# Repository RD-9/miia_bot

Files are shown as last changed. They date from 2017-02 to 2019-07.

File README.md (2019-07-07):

# Welcome MiiA Coders
Congratulations on obtaining your MiiA bot.These instructions will take you through everything you need to know on how MiiA bot is put together and what makes her tick. MiiA botis built in the form of a 3D puzzle, so the fun begins immediately. The MiiA design is based off of another great robot called Otto (https://www.ottodiy.com). We have completely open sourced the MiiA bot design under the Creative Commons  license. So without further ado, let’s jump in!
e
# CAD files
As mentioned, all the design files for Miia bot has been open sourced and can be found in the assembly folder. 
# Assembly
The cad files along with the assembly instructions is found in the assembly folder. This is to help with putting MiiA bot's physical structure together. 
# Getting started
Once the physical robot has been put together, go to the exercise folder to find the getting started guide. This will help you to connect to the Lofi Blocks programming platform and get you started quickly. 
# Exercise sheet
Once MiiA has been connected to the Lofi Blocks platform, the exercise sheets should be worked through.These exercises should be worked through with the video tutorials. This will help you to understand the steps needed when programming MiiA.It will also help you to understand the process of thinking through the problem when creating your own functions.
# Challenge
The final challenge combines all the lessons from the individual exercises. These challenges can be found in the exercise folder.New challenges will be added in order to test your robot skills, so stay tuned.

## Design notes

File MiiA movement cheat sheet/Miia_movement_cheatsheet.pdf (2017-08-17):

Movement name | Steps | Motor A | Motor B | Motor C | Motor D | loop | Notes
Motor position | | left ankle | right ankle | left hip | right hip
Output number | | output1 | output2 | output3 | output4
Stand left leg | Step 1 | 120 | 170 | 90 | 90
Stand right leg | Step 1 | 10 | 60 | 90 | 90
Walk forward (left foot step) | Step 1 | 120 | 170 | 90 | 90
| Step 2 | 120 | 170 | 120 | 120
| Step 3 | 90 | 90 | 120 | 120
Walk forward (right foot step) | step 1 | 10 | 60 | 90 | 90
| step 2 | 10 | 60 | 60 | 60
| step 3 | 90 | 90 | 60 | 60 | loop left step -right step
Walk back (left foot step) | Step 1 | 120 | 170 | 90 | 90
| Step 2 | 120 | 170 | 60 | 60
| Step 3 | 90 | 90 | 60 | 60
Walk back (right foot step) | step 1 | 10 | 60 | 90 | 90
| step 2 | 10 | 60 | 120 | 120
| step 3 | 90 | 90 | 120 | 120 | loop left step -right step
Turn left forward | Step 1 | 90 | 90 | 90 | 90
| Step 2 | 120 | 170 | 90 | 90
| Step 3 | 120 | 90 | 90 | 90
| Step 4 | 120 | 90 | 130 | 90
| Step 5 | 90 | 90 | 130 | 90
Turn left back | Step 1 | 90 | 90 | 90 | 90
| Step 2 | 120 | 170 | 90 | 90
| Step 3 | 120 | 90 | 90 | 90
| Step 4 | 120 | 90 | 50 | 90
| Step 5 | 90 | 90 | 50 | 90
Turn right forward | Step 1 | 90 | 90 | 90 | 90

| Step 2 | 10 | 60 | 90 | 90
| Step 3 | 90 | 60 | 90 | 90
| Step 4 | 90 | 60 | 90 | 50
| Step 5 | 90 | 90 | 90 | 50
Turn right back | Step 1 | 90 | 90 | 90 | 90
| Step 2 | 10 | 60 | 90 | 90
| Step 3 | 90 | 60 | 90 | 90
| Step 4 | 90 | 60 | 90 | 130
| Step 5 | 90 | 90 | 90 | 130
Hip roll forward | Step 1 | 90 | 90 | 110 | 70
| Step 2 | 90 | 90 | 90 | 90 | loop 1 and 2
Hip roll forward | Step 1 | 90 | 90 | 70 | 110 | | Each leg can be changed individually while leaving the other at 90
| Step 2 | 90 | 90 | 90 | 90 | loop 1 and 2
Foot tap left | Step 1 | 110 | 90 | 90 | 90
| Step 2 | 90 | 90 | 90 | 90 | loop 1 and 2
Foot tap right | Step 1 | 90 | 70 | 90 | 90
| Step 2 | 90 | 90 | 90 | 90 | loop 1 and 2
Foot wave right | Step 1 | 120 | 170 | 90 | 90
| Step 2 | 120 | 70 | 90 | 90
| Step 3 | 120 | 120 | 90 | 90 | loop 2 and 3
Foot wave left | Step 1 | 10 | 60 | 90 | 90
| Step 2 | 120 | 60 | 90 | 90
| Step 3 | 70 | 60 | 90 | 90 | loop 2 and 3
heal stand | Step 1 | 160 | 20 | 90 | 90
toe stand | Step 1 | 20 | 160 | 90 | 90
initial stand | Step 1 | 90 | 90 | 90 | 90

Note: input a wait of 1000 after each step

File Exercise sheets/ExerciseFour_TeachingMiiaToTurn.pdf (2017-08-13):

# Exercise four: MiiA Turning time

## Aim:

### What good is a robot that can only go straight? Not very useful I would say. This

sheet will help with that. The steps to Turn MiiA left and right will be developed.

Note: There are many ways to do this. We do it in four steps, however, you could get it down to three steps (think about the things you do when you turn you turn).

### Forward

### Turn left

| | Motor A | Motor B | Motor C | Motor D
Step one | Angle
Step two | Angle
Step three | Angle
Step four | Angle
Notes

### Turn Right

| | Motor A | Motor B | Motor C | Motor D
Step one | Angle
Step two | Angle
Step three | Angle
Step four | Angle
Notes

### Backwards

### Turn left

| | Motor A | Motor B | Motor C | Motor D
Step one | Angle
Step two | Angle
Step three | Angle
Step four | Angle
Notes

### Turn Right

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

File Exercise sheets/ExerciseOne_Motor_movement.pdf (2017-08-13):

# Exercise one: MiiA motor movements

Aim:
This sheet will help investigate the different angles and movement of the servo motors. Change the angle of the motors from 1 to 180. Write down the direction the feet and hips move.

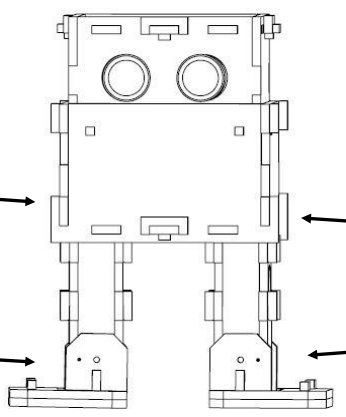
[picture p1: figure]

Foot movements
Foot | Output | Up | Down
Motor A
Motor B

Hip movements
Hips | Output | Forward | Back
Motor C
Motor D

(C)

### Left hip

(D)

### Right hip

(B)

### Right Ankle

(A)

### Left Ankle

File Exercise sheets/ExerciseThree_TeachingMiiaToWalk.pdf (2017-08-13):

# Exercise three: MiiA First steps

## Aim:

One of the first things we would want to do is getting MiiA walking. This exercise will help you make MiiA take those first steps.

## Hint: the step consists of 3 stages (Think of the way you walk, what are those stages).Important questions to ask are: How will you take 2 steps? How will you take many steps?

## Walk

### Forward – step with left leg

| | Motor A | Motor B | Motor C | Motor D
Step one | Angle
Step two | Angle
Step three | Angle
Notes

### Forward – step with Right leg

| | Motor A | Motor B | Motor C | Motor D
Step one | Angle
Step two | Angle
Step three | Angle
Notes

### Forward – Combine for two steps

| | Motor A | Motor B | Motor C | Motor D
Step one | Angle
Step two | Angle
Step three | Angle
Step four | Angle
Step five | Angle
Step six | Angle
Notes

Hint: two steps can be looped for as many steps as you want

At this point you should have gotten MiiA to walk forward. Great job!

Now to extend this to make MiiA walk back. This shouldn’t take too long. It’s the same thing, but different

## Walk Back

### Back – step with left leg

| | Motor A | Motor B | Motor C | Motor D
Step one | Angle
Step two | Angle
Step three | Angle
Notes

### Back – step with Right leg

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

### Back– Combine for two steps

| | Motor A | Motor B | Motor C | Motor D
Step one | Angle
Step two | Angle
Step three | Angle
Step four | Angle
Step five | Angle
Step six | Angle
Notes

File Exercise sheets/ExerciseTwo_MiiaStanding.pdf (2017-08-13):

# Exercise two: MiiA standing exercise

### Aim:

This sheet will help you to find the optimum angles which will make MiiA stand. Standing on one leg is the first step to many moves so it is important to ensure that the motors are in the optimum positions.

Hint: Only the two ankle servos are needed. (Motor C and D is set to 90 degrees)

Stand - Right foot

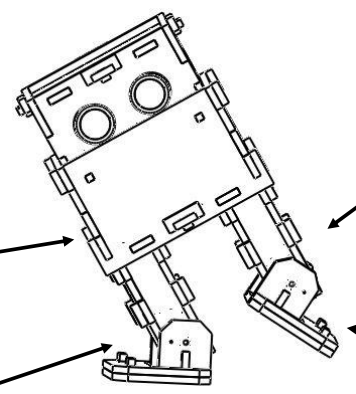
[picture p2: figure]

| Motor A | Motor B | Motor C | Motor D
Angle | | | 90 | 90
Notes

Stand - Left foot

| Motor A | Motor B | Motor C | Motor D
Angle | | | 90 | 90
Notes

(C)

### Left hip

(D)

### Right hip

(B)

### Right Ankle

(A)

### Left Ankle

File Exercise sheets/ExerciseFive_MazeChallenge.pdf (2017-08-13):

# Exercise five: MiiA Maze Challenge

Aim:
The aim of this exercise is to test the performance of the code developed.

Objective
Code the functions for your robot controller in any way you feel fit using the Lofi platform. The objective of this challenge is to navigate through a maze from one side to the other using the coded controller.

Hint: To construct the controller follow the steps in the Miia Controller construction_Exercise Five - Part 7.mp4 Video.

Instruction
- Get from the start to finish as quickly as possible
- The robot should walk over the boundaries, if this happens they should be brought back before the boundary
- The time starts once the robot has crossed the start line
- The robot can be righted if it has fallen over. However this will result in a penalty. It also should not be placed further in the maze.
- All the checkpoints should be entered before going to the finish line and time penalties will be imposed if this is not done.

Scoring
- The robot that navigates the maze the quickest wins.
- 10 seconds is added ever time the robot falls over and needs to be righted manually
- No time penalty is imposed if the robot walks over a boundary, however the robot needs to be brought back before continuing with the course.
- 2 minute is added to the time for each checkpoint not reached.

Proposed Maze

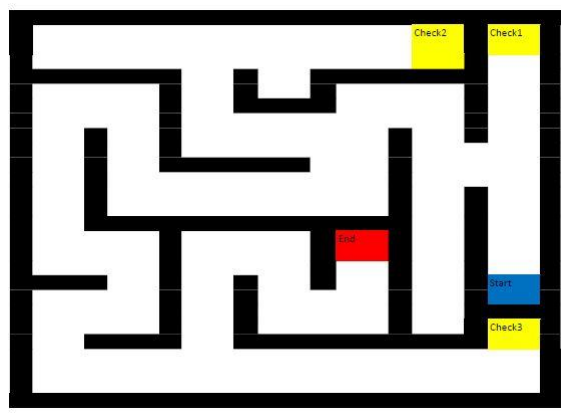
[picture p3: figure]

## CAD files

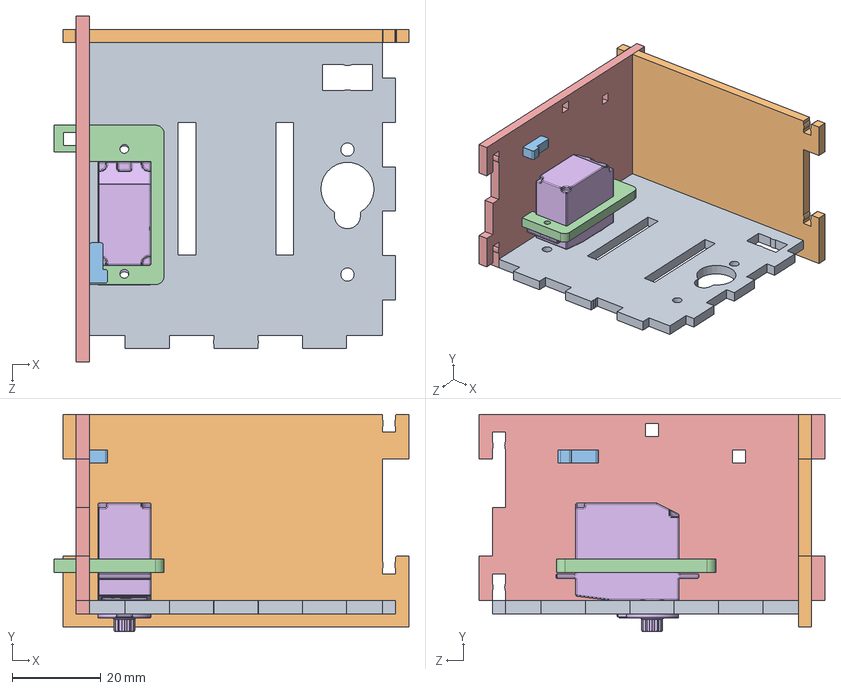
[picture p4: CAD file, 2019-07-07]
Assembly Instructions/Miia_bot_cadfiles/Bottom/Bottom_assemV2.SLDASM
80.1 x 49.0 x 78.1 mm
Bottom_bodyV2
Bottom_frontalsV2
PinGeneral
ServoMountV2
Bottom_sidesRV2
MICRO SERVO 9g

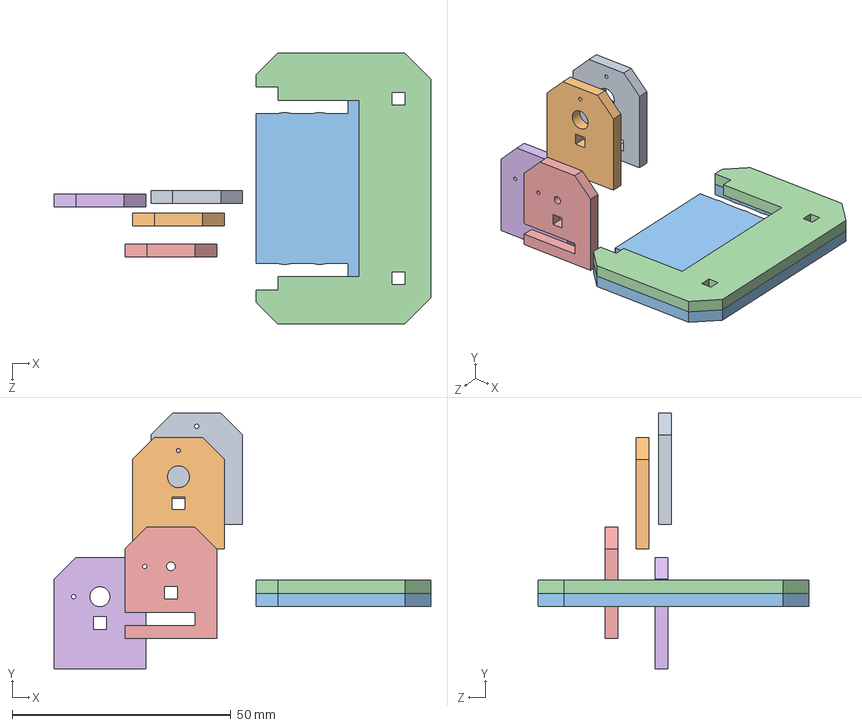
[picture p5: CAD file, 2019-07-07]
Assembly Instructions/Miia_bot_cadfiles/Foot/foot_assemV2.SLDASM
86.2 x 58.5 x 62.0 mm
backbrackethookV2
backbracketV2
Foot_botV2
foot_topV2
FrontbrackethookV2
frontbracketV2

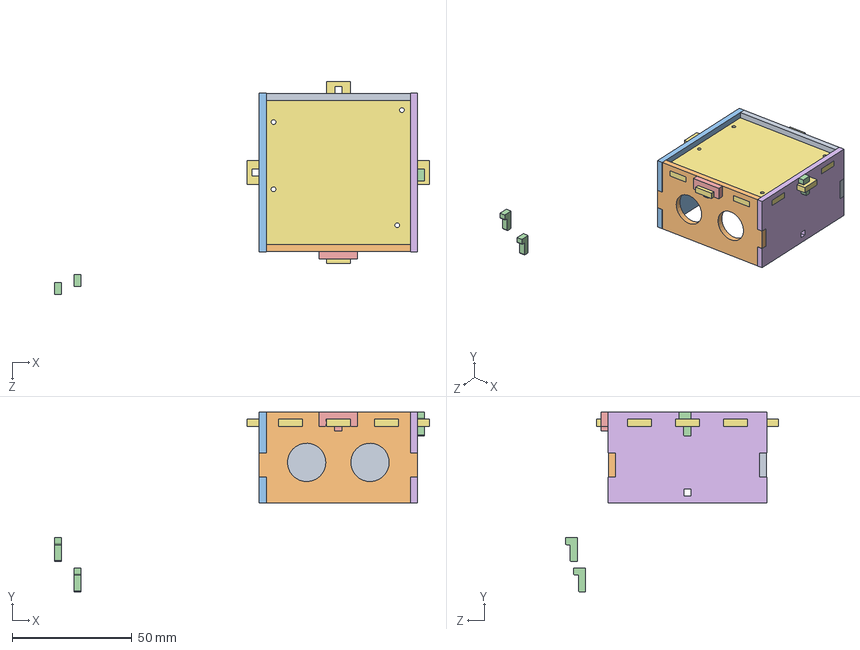
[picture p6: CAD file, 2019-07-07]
Assembly Instructions/Miia_bot_cadfiles/Head/Head_assemV2.SLDASM
156.3 x 75.0 x 88.9 mm
head_backV2
head_frontV2
head_leftV2
head_pintwoV2 x 3
head_pinV2
head_rightV2
Head_topV2

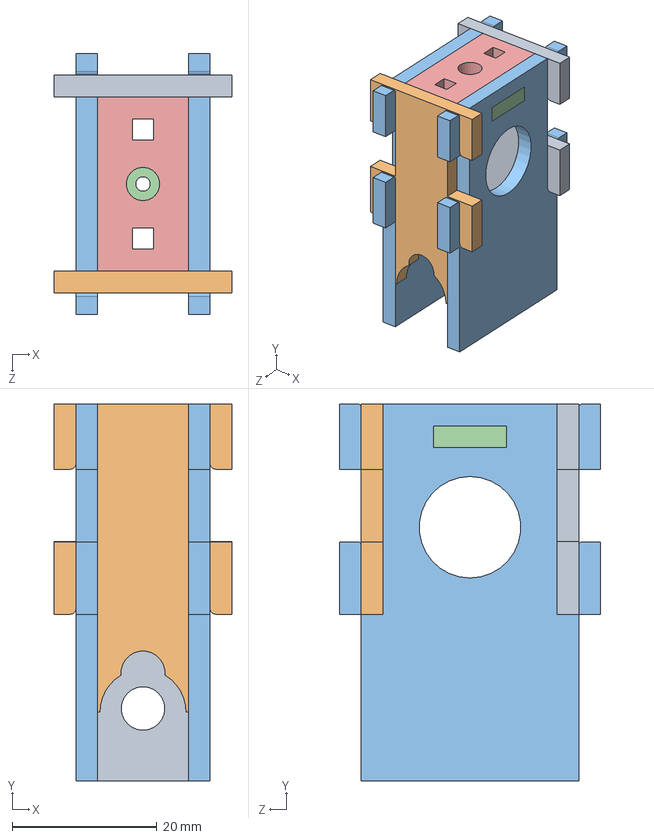
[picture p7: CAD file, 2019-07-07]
Assembly Instructions/Miia_bot_cadfiles/Legs/Leg_AssemV2.SLDASM
24.5 x 52.0 x 36.0 mm
backV2
FrontlV2
sideV2 x 2
topbotV2
topV2

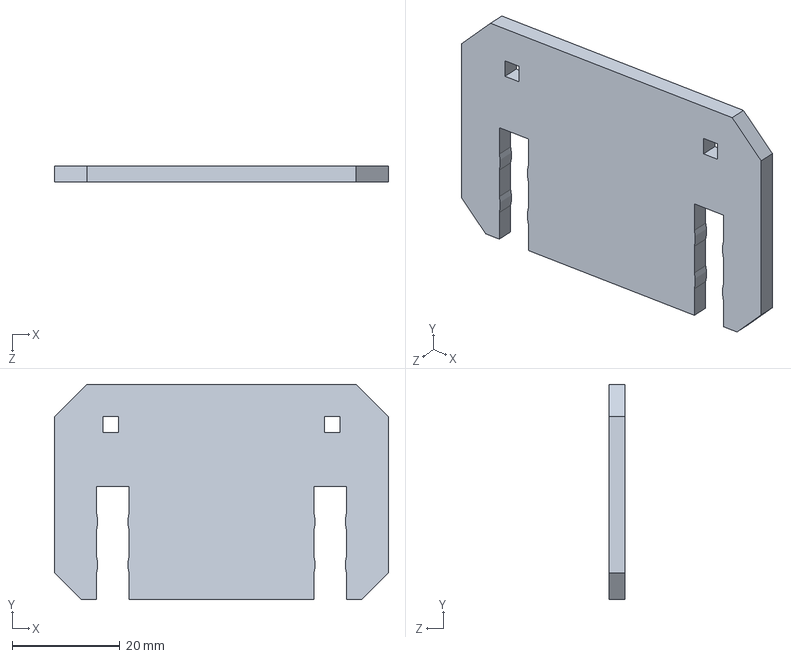
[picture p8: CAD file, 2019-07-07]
Assembly Instructions/Miia_bot_cadfiles/Foot/Foot_botV2.SLDPRT
62.0 x 40.0 x 3.00 mm

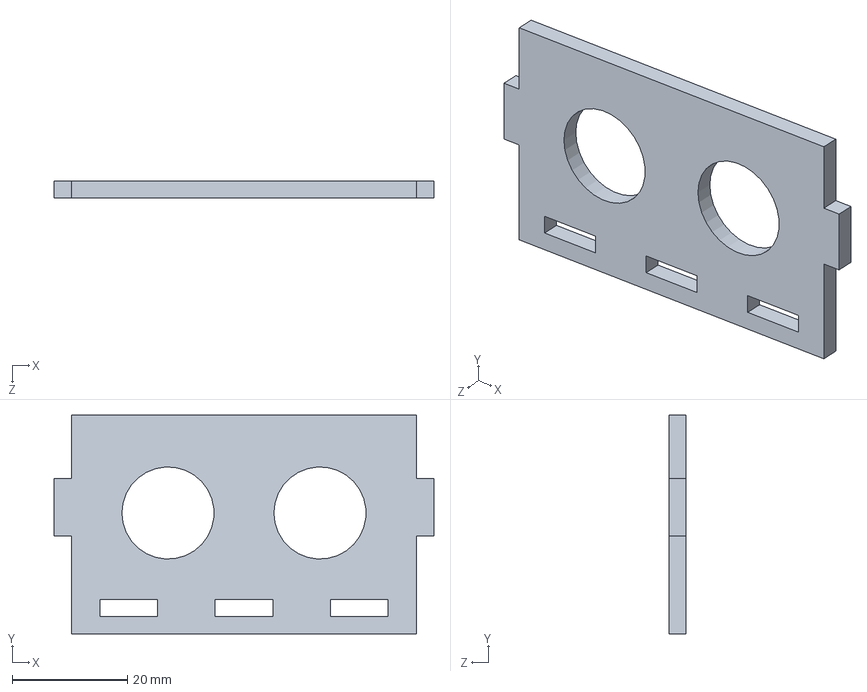
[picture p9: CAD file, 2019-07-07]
Assembly Instructions/Miia_bot_cadfiles/Head/head_frontV2.SLDPRT
66.0 x 38.0 x 3.00 mm

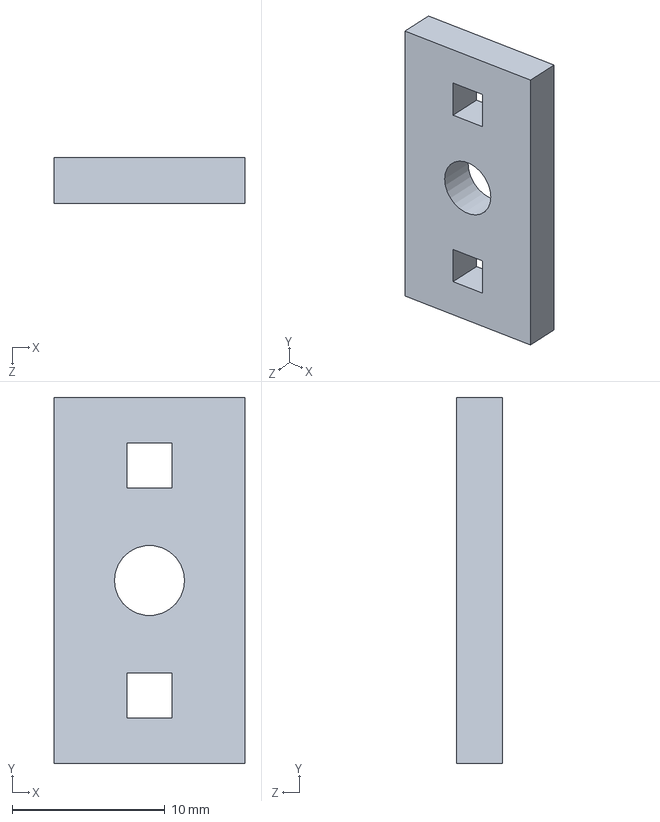
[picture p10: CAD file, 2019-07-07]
Assembly Instructions/Miia_bot_cadfiles/Legs/topV2.SLDPRT
12.5 x 24.0 x 3.00 mm

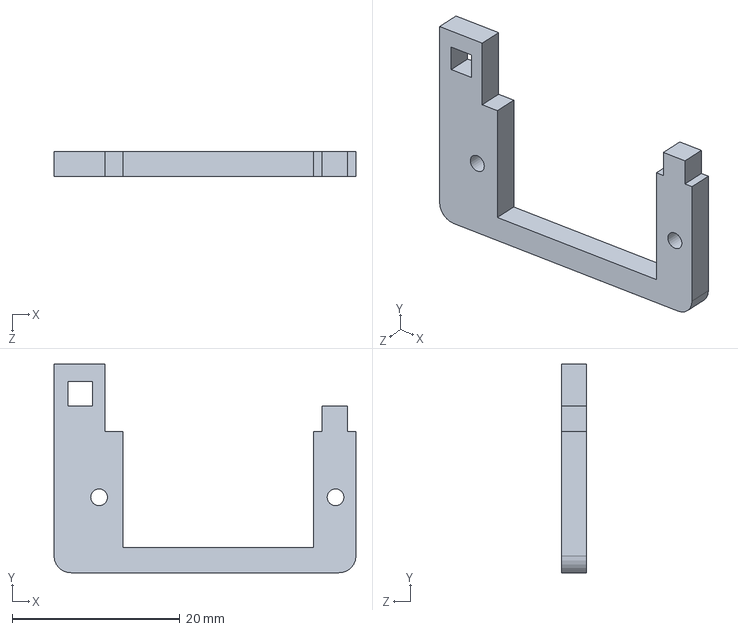
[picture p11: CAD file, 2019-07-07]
Assembly Instructions/Miia_bot_cadfiles/Bottom/ServoMountV2.SLDPRT
36.0 x 24.9 x 3.00 mm

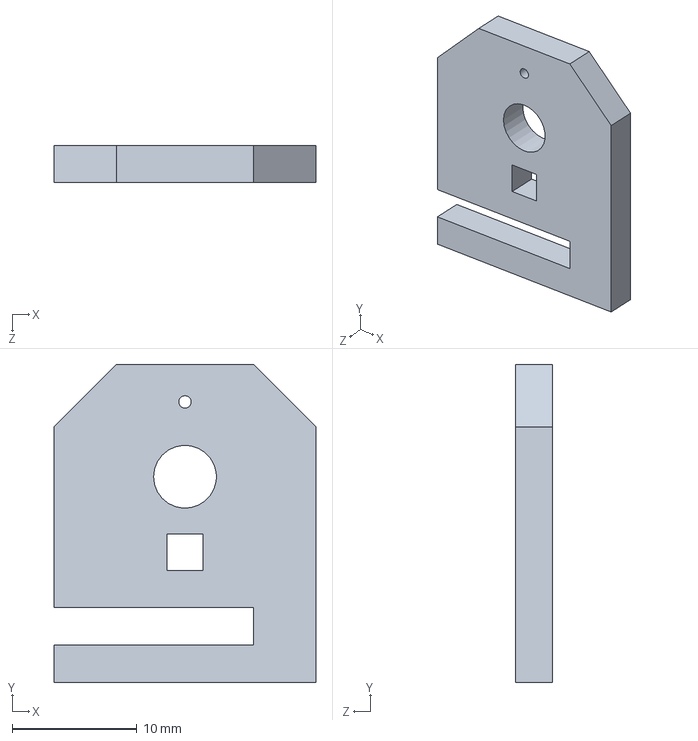
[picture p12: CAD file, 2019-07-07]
Assembly Instructions/Miia_bot_cadfiles/Foot/backbrackethookV2.SLDPRT
21.0 x 25.5 x 3.00 mm

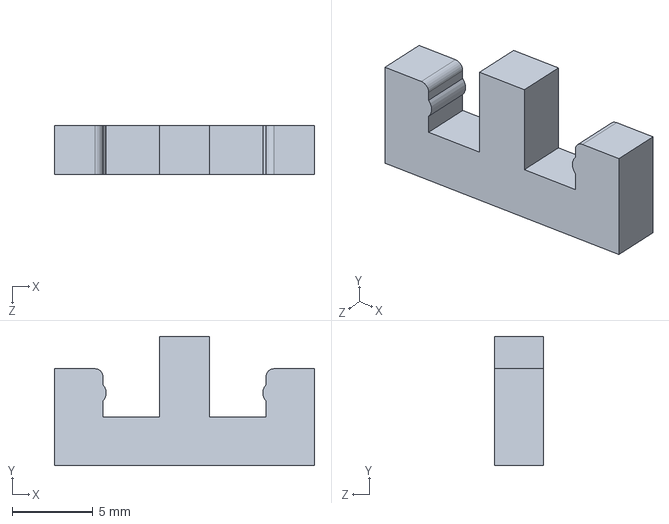
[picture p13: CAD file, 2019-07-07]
Assembly Instructions/Miia_bot_cadfiles/Head/head_pinV2.SLDPRT
16.1 x 8.00 x 3.00 mm

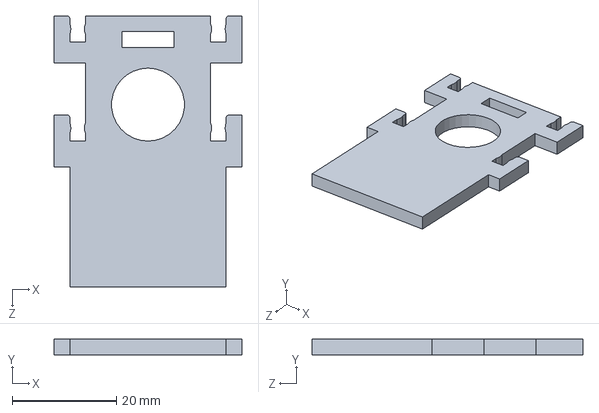
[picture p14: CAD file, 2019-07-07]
Assembly Instructions/Miia_bot_cadfiles/Legs/sideV2.SLDPRT
36.0 x 3.00 x 52.0 mm

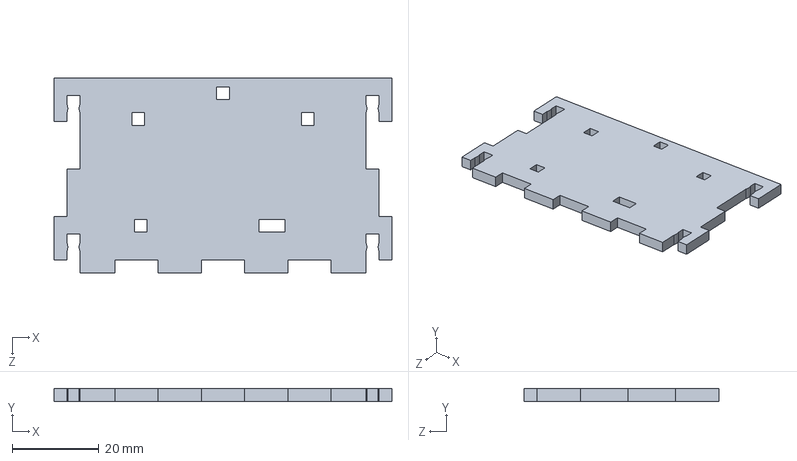
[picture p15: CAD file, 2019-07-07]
Assembly Instructions/Miia_bot_cadfiles/Bottom/Bottom_sidesRV2.SLDPRT
78.1 x 3.00 x 45.0 mm

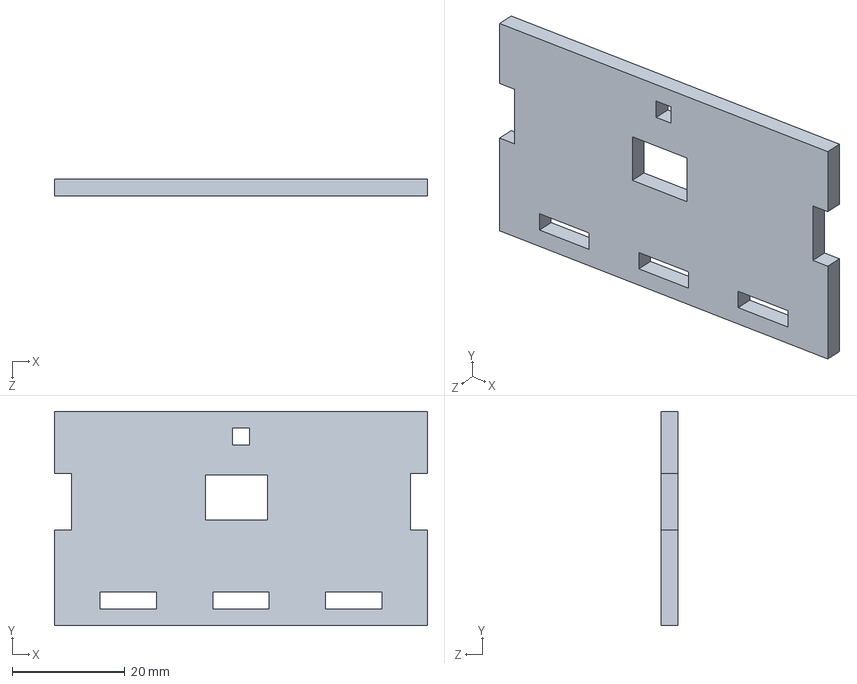
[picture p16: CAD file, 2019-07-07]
Assembly Instructions/Miia_bot_cadfiles/Head/head_leftV2.SLDPRT
66.1 x 38.0 x 3.00 mm

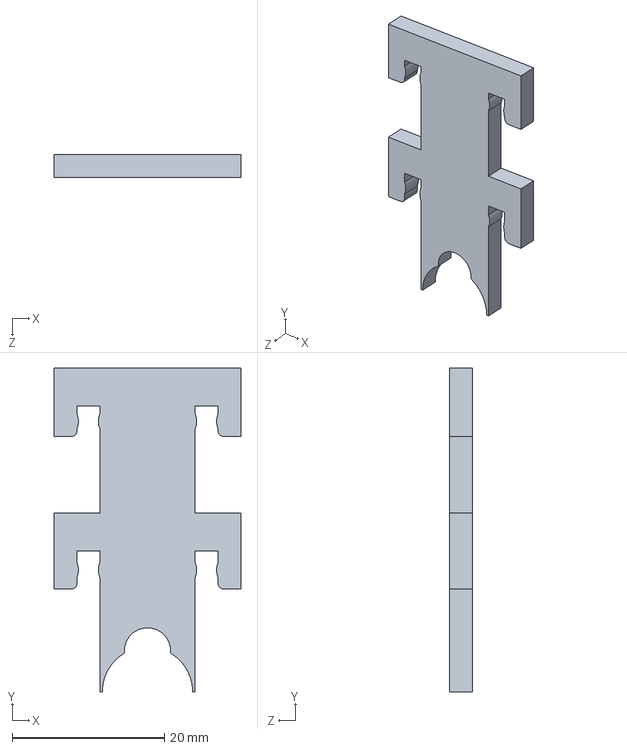
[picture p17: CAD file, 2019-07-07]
Assembly Instructions/Miia_bot_cadfiles/Legs/FrontlV2.SLDPRT
24.5 x 42.5 x 3.00 mm

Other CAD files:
Assembly Instructions/Miia_bot_cadfiles/Bottom/Bottom_bodyV2.SLDPRT
Assembly Instructions/Miia_bot_cadfiles/Foot/frontbracketV2.SLDPRT
Assembly Instructions/Miia_bot_cadfiles/Head/head_pintwoV2.SLDPRT
Assembly Instructions/Miia_bot_cadfiles/Legs/topbotV2.SLDPRT
Assembly Instructions/Miia_bot_cadfiles/Bottom/Bottom_frontalsV2.SLDPRT
Assembly Instructions/Miia_bot_cadfiles/Bottom/PinGeneral.SLDPRT
Assembly Instructions/Miia_bot_cadfiles/Bottom/PinGeneralV2.SLDPRT
Assembly Instructions/Miia_bot_cadfiles/Drawing/Manufacture.SLDDRW
Assembly Instructions/Miia_bot_cadfiles/Foot/FrontbrackethookV2.SLDPRT
Assembly Instructions/Miia_bot_cadfiles/Foot/backbracketV2.SLDPRT
Assembly Instructions/Miia_bot_cadfiles/Foot/foot_topV2.SLDPRT
Assembly Instructions/Miia_bot_cadfiles/Head/Head_topV2.SLDPRT
Assembly Instructions/Miia_bot_cadfiles/Head/head_backV2.SLDPRT
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

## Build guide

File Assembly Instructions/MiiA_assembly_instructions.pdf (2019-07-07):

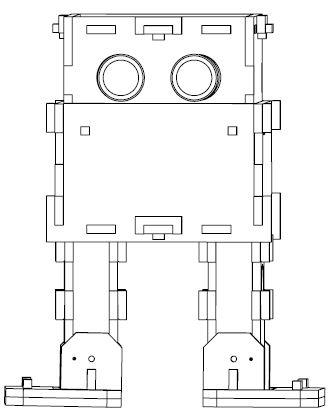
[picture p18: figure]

# MIIA ASSEMBLY INSTRUCTIONS

### WELCOME

Congratulations! You are now the proud new owner of your own MiiA robot. These instructions will take you through everything you need to know on how MiiA is put together and what makes her tick. MiiA is built in the form of a 3D puzzle, so the fun begins immediately. The MiiA bot design is based off another great robot called Otto bot (https://www.ottodiy.com). So, without further ado, let’s jump in!

## Contents

## What’s in the Box

All parts included in the kit are shown in this section.

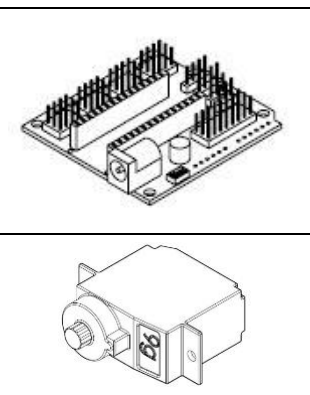
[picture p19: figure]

Part | Preview | Part | Preview
Battery holder (1x) | | Arduino shield (1x)
HC06 Bluetooth transceiver (1x) | | Servo Motor (4x)

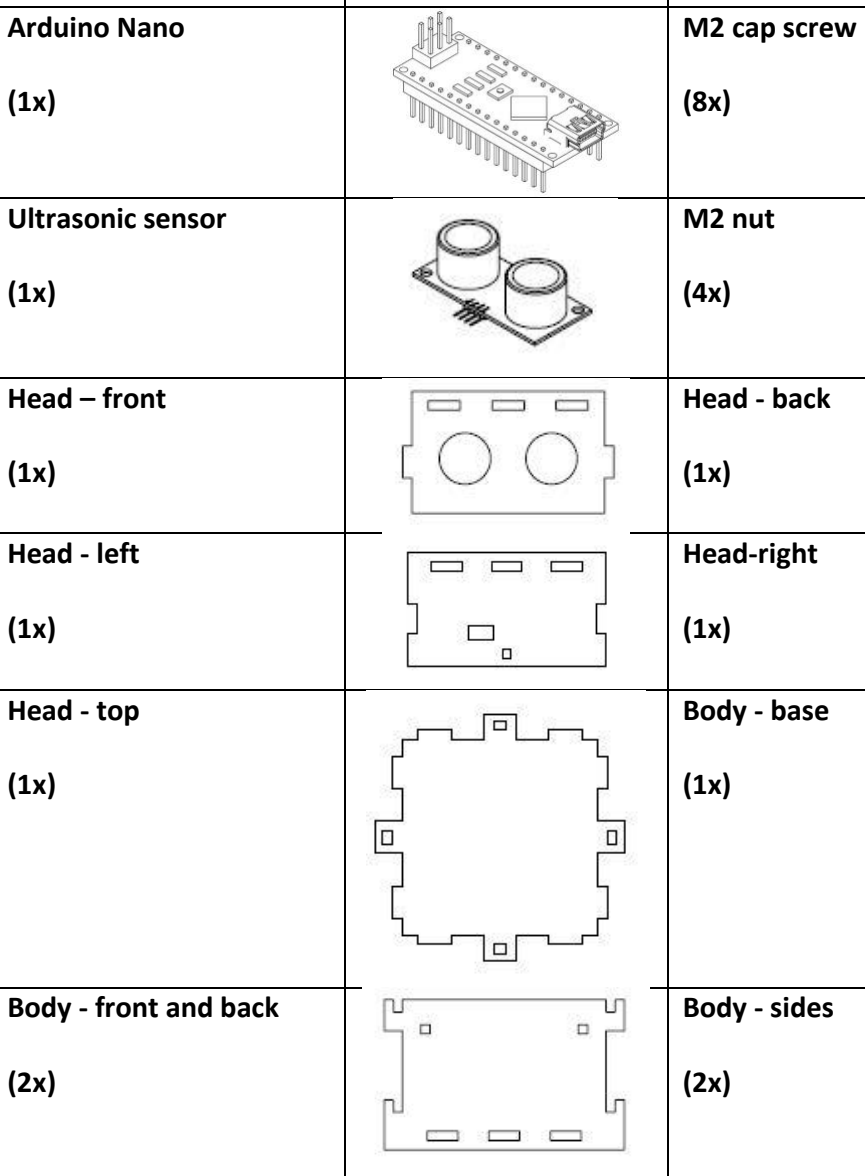
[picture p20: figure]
Arduino Nano (1x); M2 cap screw (8x); Ultrasonic sensor (1x); M2 nut (4x); Head – front (1x); Head - back (1x); Head - left (1x); Head-right (1x); Head - top (1x); Body - base (1x)
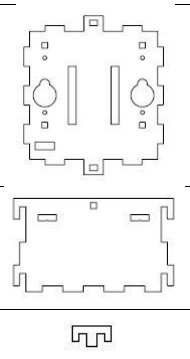
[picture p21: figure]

Body - front and back (2x) | | Body - sides (2x)
Body - corners (4x) | | Head and body pin (6x)

General pin (12x) | Leg - top (2x)
Leg - bottom plate (2x) | Leg - front (2x)

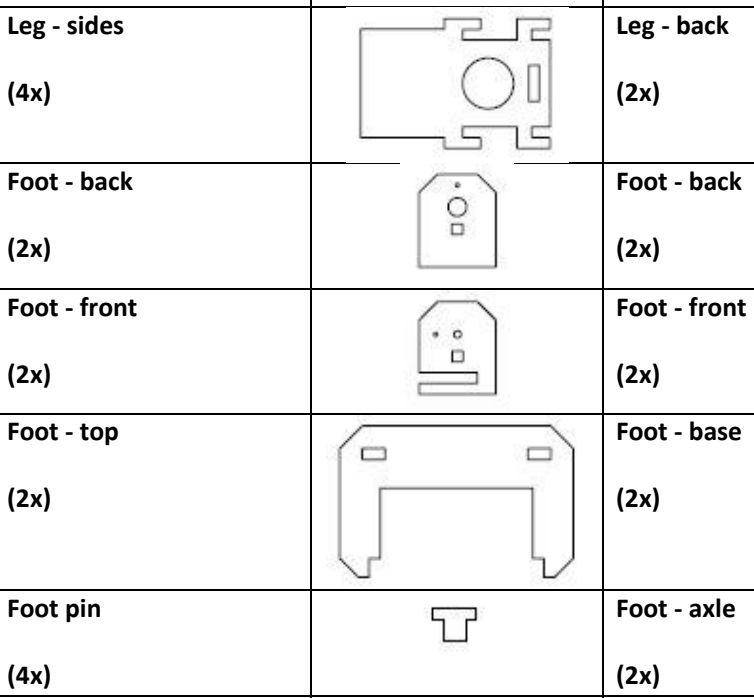
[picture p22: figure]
Leg - sides (4x); Leg - back (2x); Foot - back (2x); Foot - front (2x); Foot - top (2x); Foot - base (2x); Foot pin (4x); Foot - axle (2x)
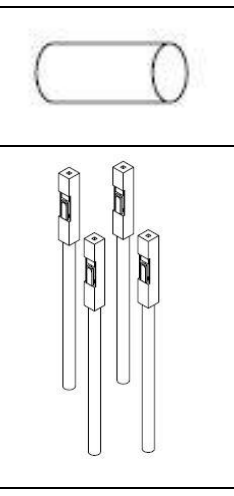
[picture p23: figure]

USB mini cable (1x) | Jumper cables (8x)

Nut holder (4x)

## Putting MiiA Together

This section describes how to assemble the individual parts that make up MiiA.

### Head

Part | Preview | Part | Preview

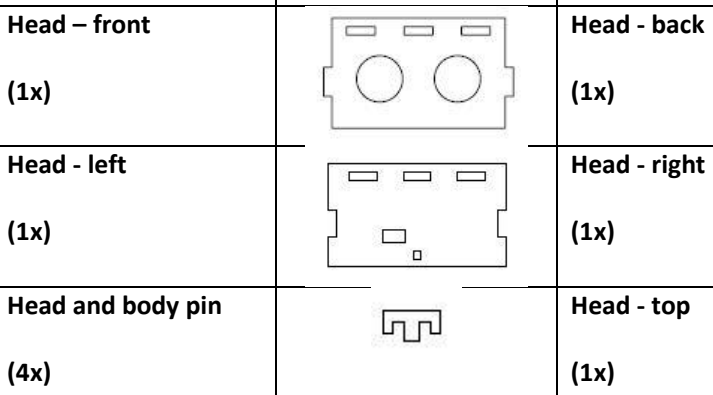
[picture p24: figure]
Head – front (1x); Head - back (1x); Head - left (1x); Head - right (1x); Head and body pin (4x); Head - top (1x)
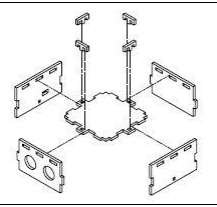
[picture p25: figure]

How to assemble

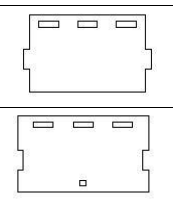
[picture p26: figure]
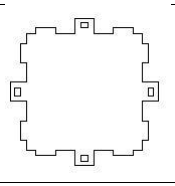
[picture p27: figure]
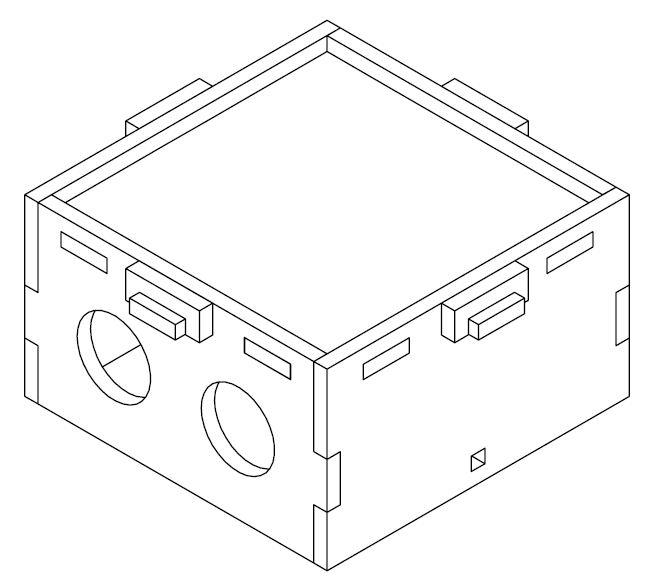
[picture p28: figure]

### Body

Part | Preview | Part | Preview
Body - front and back (2x) | | Body – sides (2x)

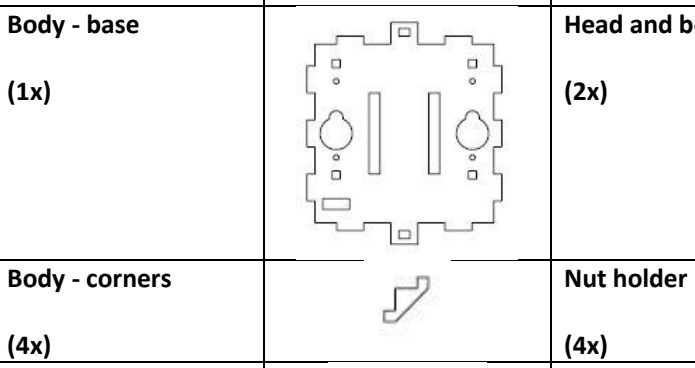
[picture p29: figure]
Body - corners (4x); Nut holder (4x)

Body - base (1x) | | Head and body pin (2x)

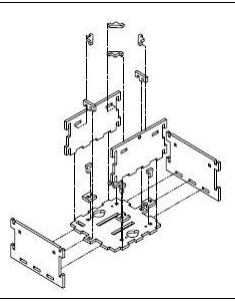
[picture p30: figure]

General pin (4x)

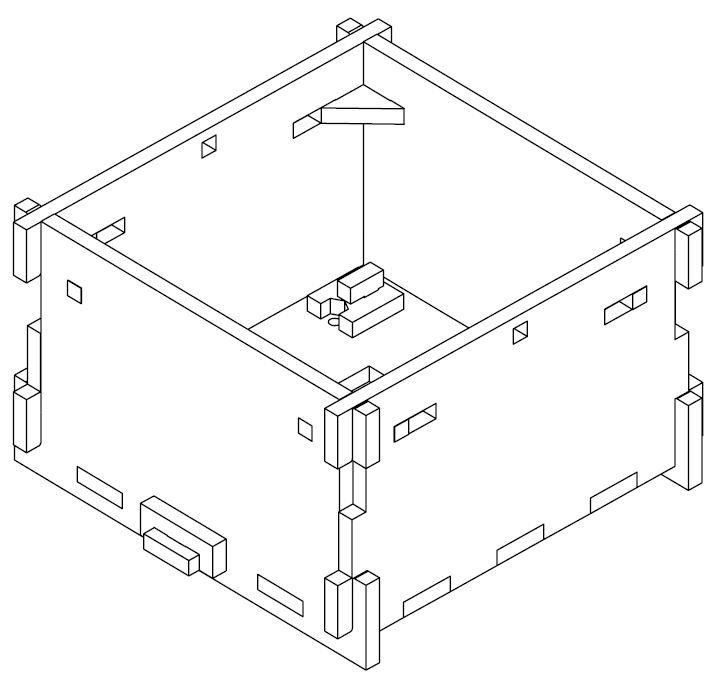
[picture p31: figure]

How to assemble

### Legs

Part | Preview | Part | Preview
General pin (4x) | | Leg - top (2x)
Leg - bottom plate (2x) | | Leg - front (2x)

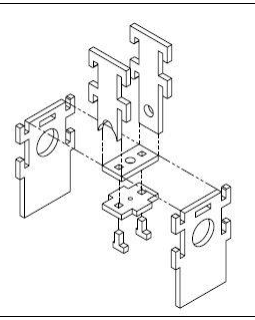
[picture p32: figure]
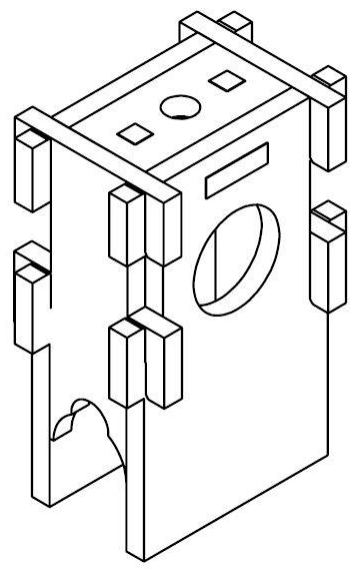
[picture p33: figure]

Leg - sides (4x) | | Leg - back (2x)

How to assemble

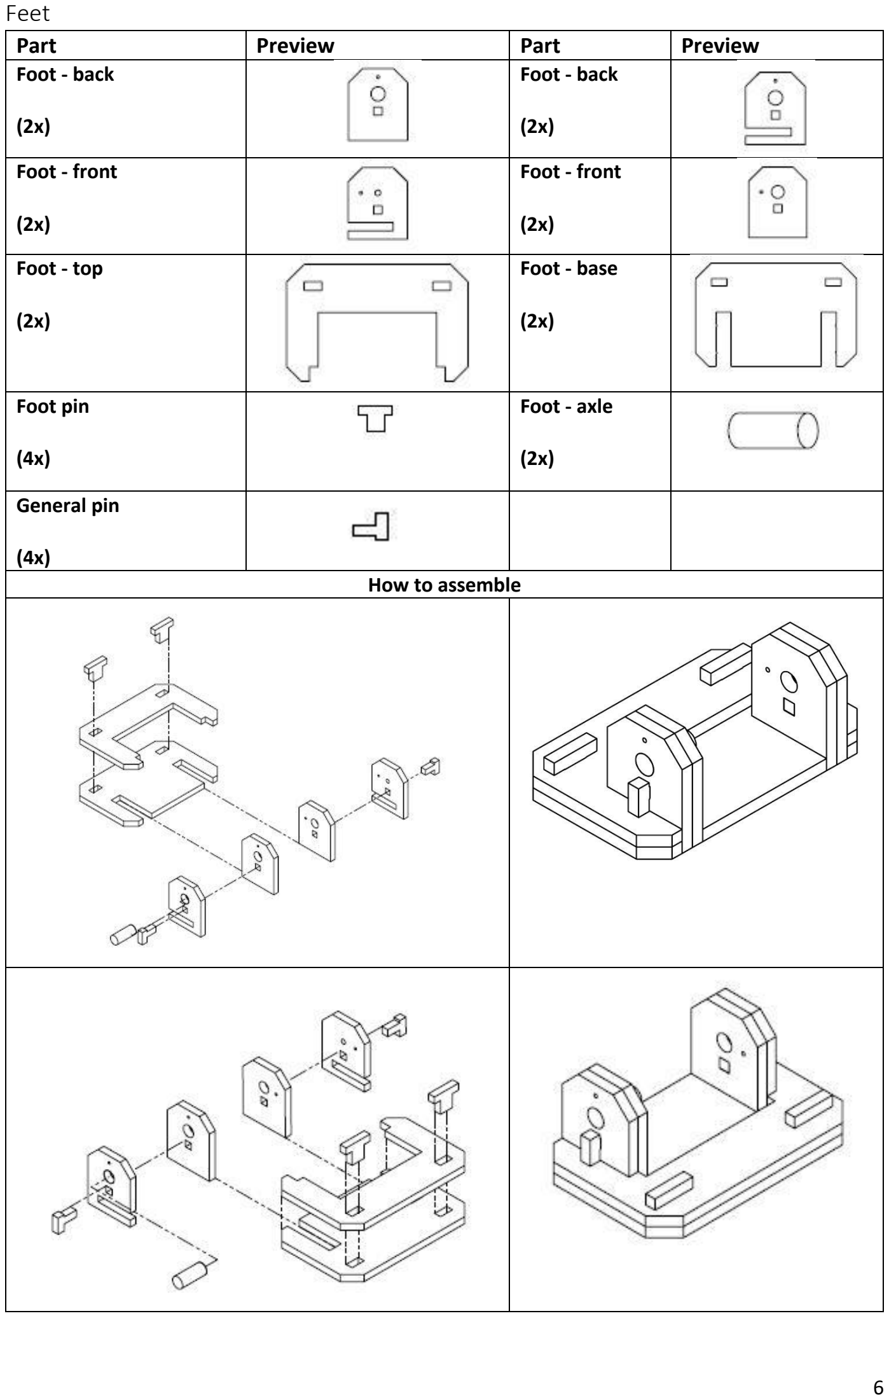
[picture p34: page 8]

### Feet

Part | Preview | Part | Preview
Foot - back (2x) | | Foot - back (2x)
Foot - front (2x) | | Foot - front (2x)
Foot - top (2x) | | Foot - base (2x)
Foot pin (4x) | | Foot - axle (2x)

General pin (4x)

How to assemble

## Motor Calibration

When inserting motors into the robot, please ensure that the servo motors have been set to 90 degrees. Have a look at our calibration video here. (https://www.youtube.com/watch?v=F62Hy-xyzCg) You can also find our calibration code here. (https://github.com/RD-9/miia_bot/blob/master/Sample%20Code/miia_calibration.ino)

## Assembly

This section shows how to install the motors that make MiiA move.

Description | Assembly Instruction

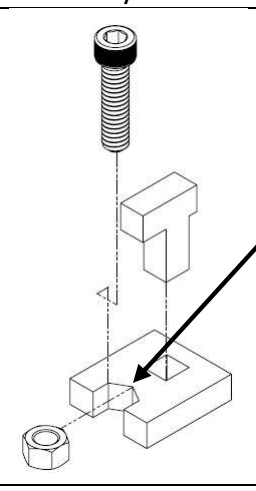
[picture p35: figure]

Nut holder assembly | 1 drop of glue to fix nut in place

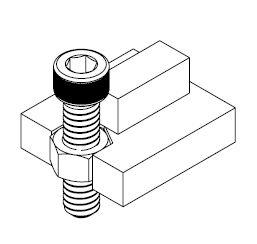
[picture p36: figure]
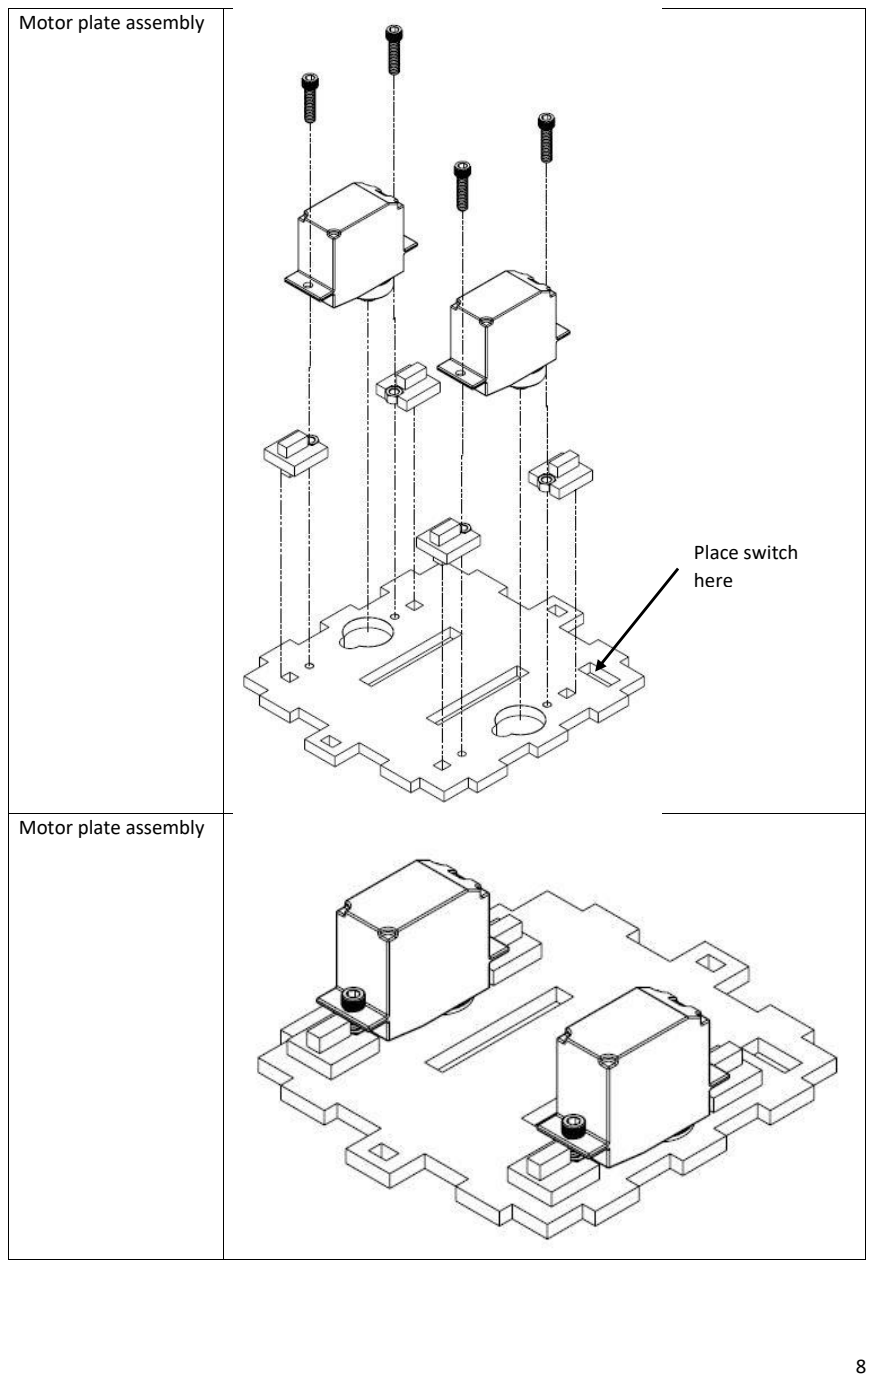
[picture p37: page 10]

Motor plate assembly

Motor plate assembly

Place switch
here

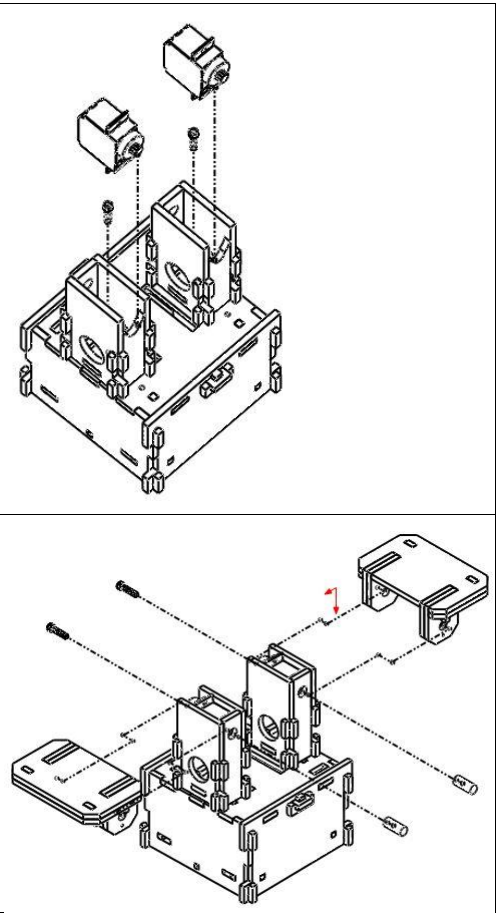
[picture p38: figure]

Leg plate assembly

Feet assembly

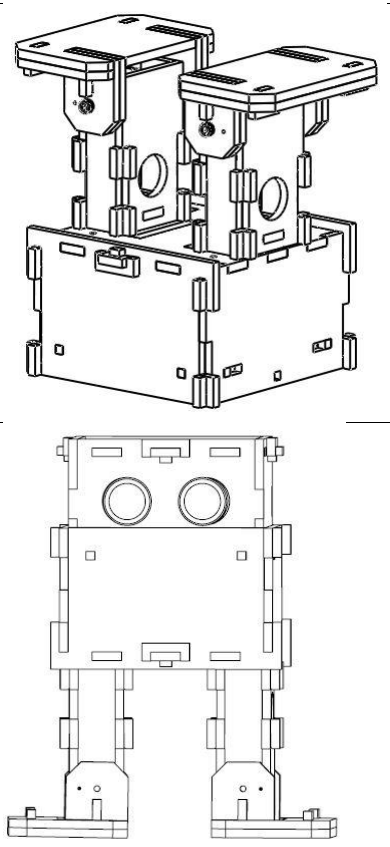
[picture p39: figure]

Complete bottom
body assembly

Complete assembly

11

## Electrical Connections

By connecting all the electrical component as shown below, MiiA will be able to be programmed and controlled to move.

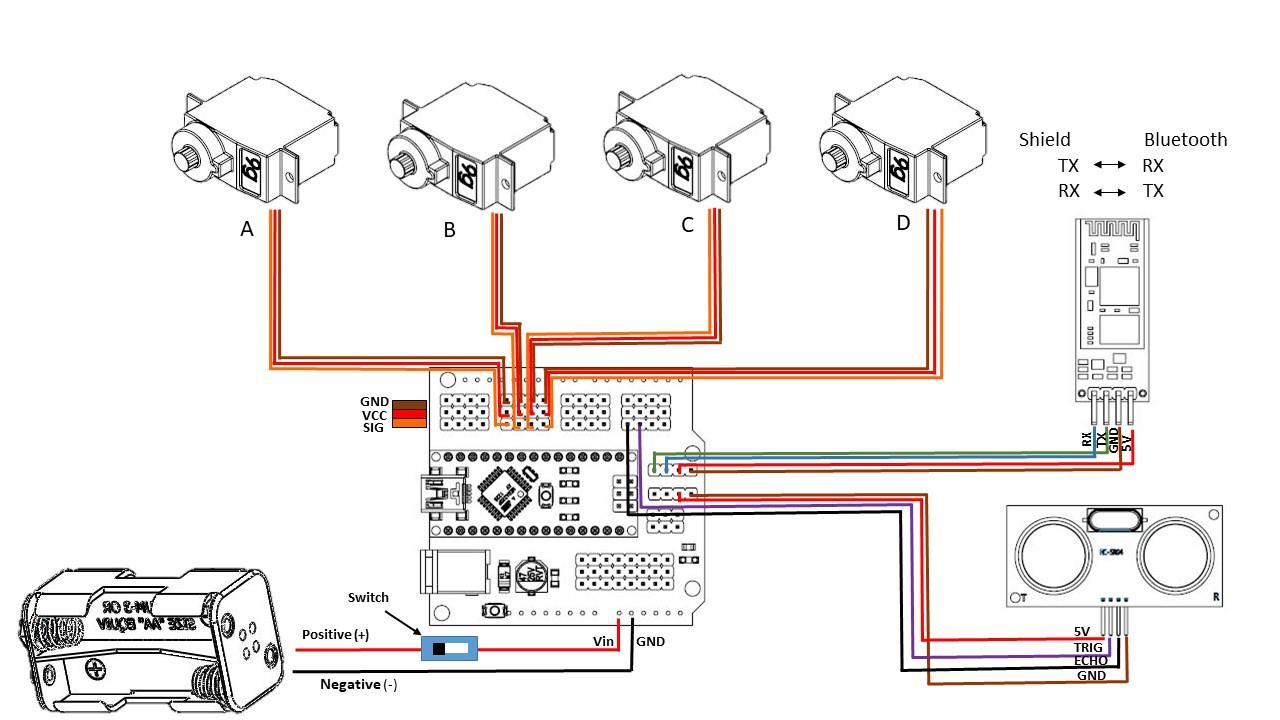
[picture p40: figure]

## Final Assembly

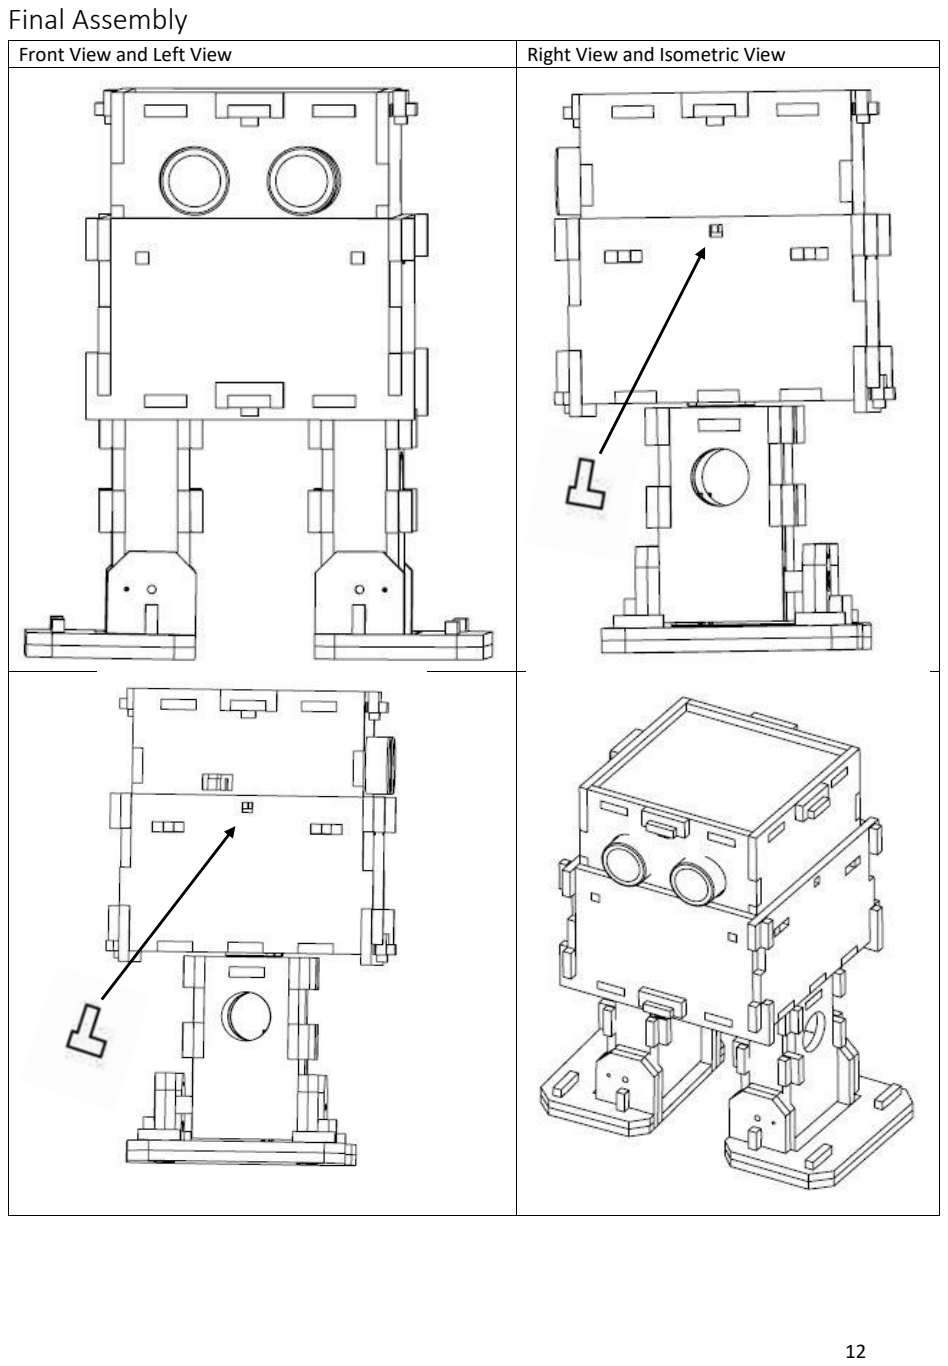
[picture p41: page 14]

Front View and Left View | Right View and Isometric View

Well Done! MiiA is now complete and ready to be programmed.

To start your robotics journey please go to our website (http://miiabot.rd-9.co.za/learn/) for instructions on getting started with programming her.

If you are having any issues with the kits, please do not hesitate to contact us at info@rd-9.co.za

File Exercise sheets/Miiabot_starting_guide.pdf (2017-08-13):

# Start: Getting Coding with MiiA

### Introduction

At this stage you should have MiiA bot fully assembled and ready for programming. If you are a beginner this guide will help you set things up and get you started quickly.

MiiA uses an easy to program drag and drop system which has been developed by LOFI Blocks (http://www.lofiblocks.com/code/). The drag and drop system uses Bluetooth to communicate with the MiiA bot. Lofi Blocks allows you to program your robot using an App (android or IOS) or through chrome with use of a chrome extension. The process of setting MiiA bot up is explained in the steps below:

### Step one: Downloading the Arduino platform

This is the programming platform that is used to load the Lofi firmware/brain code with the microcontroller. The Arduino IDE or platform can be downloaded here: https://www.arduino.cc/en/Main/Donate

### Step two: Downloading the LOFI code from our website

Next the code/firmware that enables the LOFI system to communicate with the MiiA bot needs to be downloaded here: https://github.com/RD-9/miia_bot

Note: There is firmware code that is available on the LOFI Blocks website, however this will not work with MiiA. Therefore please download the code from the link above.

Once open it may seem a bit overwhelming. Please don’t be alarmed, at this point you do not need to understand what is going on in the code, all that needs to be done is to upload this code to the microcontroller.

### Step three: uploading firmware to the microcontroller

The next step is to upload or flash the code onto the microcontroller board. To do this open the code which was downloaded and plug in the board using the USB cable provided (make sure the switch is off).

Next we want to choose the correct port and microcontroller. In the downloaded Arduino platform go to:

Tools -> board -> Arduino Nano

The next step is to check the port which has been assigned to the Arduino board. This is done by going to:

Control panel -> device manager-> Ports (COM & LPT)

In this drop down menu, the port number that the microcontroller is connected to can be seen. Go back to the Arduino IDE and navigate to:

Tools -> Port-> *pick the port which is connected to the board*

The code is now ready to be flashed onto the board.

Click the upload key (arrow pointing right) and wait for the program to complete the upload process.

Congratulations. The code is now on your board and is now ready to use. Disconnect the USB cable and switch on the robot at the switch.

### Step four: Pairing with the Bluetooth module

The next step is to pair the Bluetooth module to your computer. To do this make sure that the robot is on and that the Bluetooth module chip is flashing. Go to Bluetooth & other devices. Wait for the Bluetooth module to be detected, the name will be HC-06. Click pair with this device. If prompted for a password use 1234 or 0000. Once the module is paired you are ready to move on to the next step.

### Step five: Setting up coding environment with chrome

The next step is to connect with the LOFI coding environment with chrome. First go to the coding website here: http://www.lofiblocks.com/code/.

Before you will be able to use the chrome platform the LOFI Blocks chrome extension needs to be downloaded. This can be found here: https://chrome.google.com/webstore/detail/lofi-robotextension/opdjdfckgbogbagnkbkpjgficbampcel?hl=en (https://chrome.google.com/webstore/detail/lofi-robot-extension/opdjdfckgbogbagnkbkpjgficbampcel?hl=en)

Download and install the program.

Once installed run the program. With the computer still paired with the Bluetooth module, follow the same process as before to check the port the Bluetooth module is connected to. Choose this serial port in the drop down menu of the Lofi code extension and click connect.

In the Chrome code editor the robot head should now have a ring around it. If that is the case, you are now ready to start coding.

Work through the exercise sheets found here https://github.com/RD-9/miia_bot (https://github.com/RD-9/miia_bot)

Happy Coding!

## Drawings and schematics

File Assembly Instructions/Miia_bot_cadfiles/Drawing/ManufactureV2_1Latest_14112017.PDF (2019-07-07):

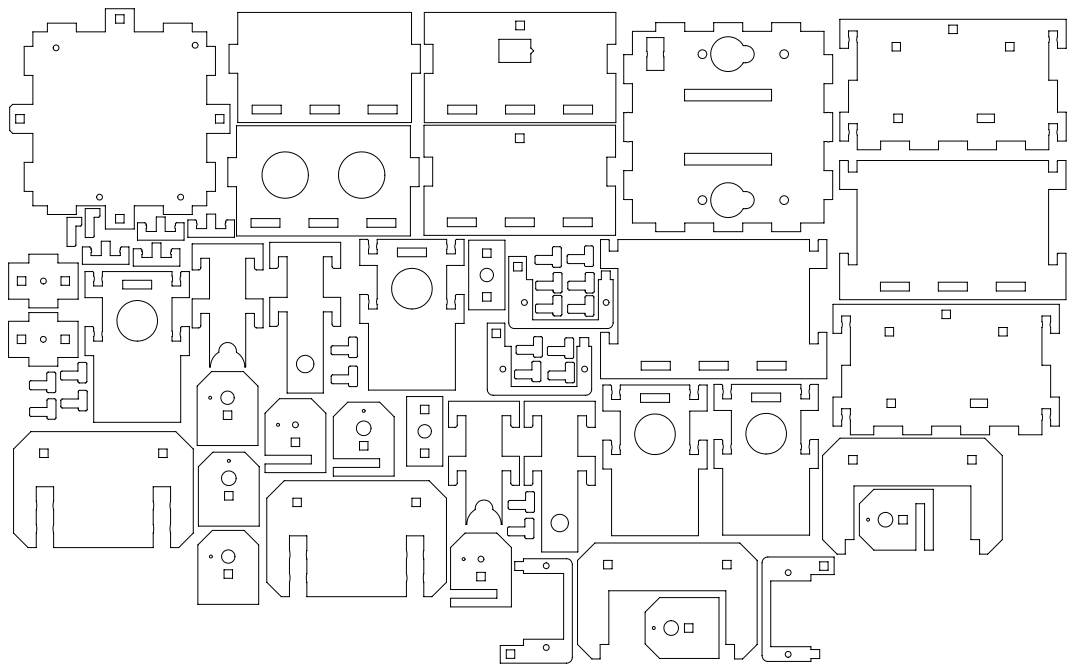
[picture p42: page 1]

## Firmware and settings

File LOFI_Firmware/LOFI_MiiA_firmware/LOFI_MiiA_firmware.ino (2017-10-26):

// LOFI Brain firmware to communicate with LOFI Robot ScratchX Chrome Plugin
// USB + Bluetooth version
// Author: Maciej Wojnicki
// WWW.LOFIROBOT.COM

/*
 * Lofi firmware developed for MiiA bot. 
 * Version v1.2
 * Date: 17/10/2017
 * Instructions: 
 * Connect your Arduino using the usb cable. 
 * Set the board to the arduino board, in the arduino ide go to:
 * tools -> board -> arduino Nano
 * Connect port:
 * tools -> port -> choose port board is connected to
 * click the upload button(use the second button from the left above, arrow pointing right)
 * ******************************************************************
 * Electronic Connections:
 * ******************************************************************
 * While facing the front of MiiA:
 * 
 * Left Hip Servo - 8
 * Right Hip Servo - 9
 * Left Foot Servo - 10
 * Right Foot Servo - 11
 * UltraSonic Sensor TrigPin - 2
 * UltraSonic Sensor EchoPin - 3
 * Bluetooth Module TX - 0 (RX)
 * Bluetooth Module RX - 1 (TX)
 * Servo to Calibrate - A0
 */

// included libraries
#include <Servo.h>

// function prototypes
void set_servo_position(Servo my_servo, int pin, int pos);
void calibrate(Servo my_servo, int pos);
void servo_off(Servo my_servo);
void configure_pins();

// pin assignments
#define left_hip_servo_pin 8
#define right_hip_servo_pin 9
#define left_foot_servo_pin 10
#define right_foot_servo_pin 11
#define servo_calibration_pin A0
#define uss_trigger_pin 2
#define uss_echo_pin 3

// constants
#define baud_rate 57600 // nb baud rate must be 57600 for LoFi Blocks
#define servo_calibration_pos 90

// create servo objects
Servo servo_calibrate;
Servo servo_left_hip;
Servo servo_right_hip;
Servo servo_left_foot;
Servo servo_right_foot;

//data sending (arduino->computer) interval  
//raise it if you encouter communication jitter
const long interval = 10000;

int current_byte = 0;
int prev_byte = 0;
int analog1 = 1;
int analog2 = 2;
int analog3 = 3;
int analog4 = 4;

unsigned long previousMillis = 0;
unsigned long currentMillis;

void setup() 
{
  // initialize serial communications at specified baud rate
  Serial.begin(baud_rate);

  // configure all pin modes
  configure_pins();

  // set calibration pin and drive pin to calibrated position
  servo_calibrate.attach(servo_calibration_pin);
  calibrate(servo_calibrate, servo_calibration_pos);

  // setup complete
}

void loop() 
{
  currentMillis = millis();

  //receiving data from ScratchX Chrome plugin
  receiving();

  // timer delay reduce data bandwidth
  if (currentMillis - previousMillis >= interval) 
  {
    
    previousMillis = currentMillis;

    //sending data to ScratchX Chrome plugin
    sending();
  }
}

long odleglosc() 
{
  
  long duration, distance;
  digitalWrite(uss_trigger_pin, LOW); 
  delayMicroseconds(2); 
  digitalWrite(uss_trigger_pin, HIGH);
  delayMicroseconds(10); 
  digitalWrite(uss_trigger_pin, LOW);
  duration = pulseIn(uss_echo_pin, HIGH);
  distance = (duration/2)/29.1;
  return distance;  
}

void receiving() 
{
  if (Serial.available() > 0) 
  {
  current_byte = Serial.read();    
  outputs_set();
  prev_byte = current_byte;
  } 
}

void outputs_set() 
{
    //servo output1
    if (prev_byte == 208) 
    {
      set_servo_position(servo_left_hip, left_hip_servo_pin, current_byte);      
    }
      //servo output2
    if (prev_byte == 209) 
    {
      set_servo_position(servo_right_hip, right_hip_servo_pin, current_byte);
    }
      //servo output3
    if (prev_byte == 210) 
    {
      set_servo_position(servo_left_foot, left_foot_servo_pin, current_byte);
    }
      //servo output4
    if (prev_byte == 211) 
    {
      set_servo_position(servo_right_foot, right_foot_servo_pin, current_byte);
    }

    if (prev_byte == 212 && current_byte == 99) 
    {
      // detach all servos
      servo_off(servo_left_hip);
      servo_off(servo_right_hip);
      servo_off(servo_left_foot);
      servo_off(servo_right_foot);      
    }
}

void sending() {

  // even if not using analog inputs, LoFi requires this.
  Serial.write(224);
  Serial.write(byte(analog1));
  Serial.write(225);
  Serial.write(byte(analog2));
  Serial.write(226);
  Serial.write(byte(analog3));
  Serial.write(227);
  Serial.write(byte(analog4));
  Serial.write(240);

  // ultra sonic sensor output
  Serial.write(byte(odleglosc()));   
  // last byte "i" character as a delimiter for BT2.0 on Android
  Serial.write(105);  
}

// function to configure pins and pin modes
void configure_pins()
{
  // servo calibration pin
  pinMode(servo_calibration_pin, OUTPUT);
  
  // miia servo motor signal pins
  pinMode(left_hip_servo_pin, OUTPUT);  
  pinMode(right_hip_servo_pin, OUTPUT);
  pinMode(left_foot_servo_pin, OUTPUT);
  pinMode(right_foot_servo_pin, OUTPUT);

  // ultrasonic sensor trigger and echo pins
  pinMode(uss_trigger_pin, OUTPUT);
  pinMode(uss_echo_pin, INPUT);
}

// function to turn off, and detach, all a servo
void servo_off(Servo my_servo) 
{
  my_servo.detach();
}

// function to calibrate servo motors to predtermined position
void calibrate(Servo my_servo, int pos)
{
  my_servo.write(pos);
  delay(15);
}

// function to set position of a servo motor
void set_servo_position(Servo my_servo, int pin, int pos)
{
  my_servo.attach(pin);
  if (pos < 15)
  {
    my_servo.write(15);
  }
  else
  {
    my_servo.write(pos);
  }
}

//end

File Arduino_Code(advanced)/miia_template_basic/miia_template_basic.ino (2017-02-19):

//Included libraries here
#include <Servo.h>

//Define servo motor objects
Servo myservo_0; //left  ankle
Servo myservo_1; //right ankle
Servo myservo_2; //left  hip
Servo myservo_3; //right hip

// constant definitions

// change pins according to which servos are connected where
#define LEFT_FOOT A0
#define RIGHT_FOOT A1
#define LEFT_HIP A2
#define RIGHT_HIP A3

//Define global variables 

//Function declarations
void example_Function();

void setup() {
  
  //Put your setup code here, to run once:
  Serial.begin(9600);
   
  //Click Ctrl+shift+M to see serial monitor
  Serial.println("Start of Code..."); 
  
  //configure pin modes
  pinMode(LEFT_FOOT, OUTPUT);
  pinMode(RIGHT_FOOT, OUTPUT);
  pinMode(LEFT_HIP, OUTPUT);
  pinMode(RIGHT_FOOT, OUTPUT);
  
  // configure servos
  myservo_0.attach(LEFT_FOOT);  // attaches the servo on pin 9 to the left leg
  myservo_1.attach(RIGHT_FOOT); //attaches the servo on pin 10 to the right leg  
  myservo_2.attach(LEFT_HIP);  // attaches the servo on pin 11 to the left hip
  myservo_3.attach(RIGHT_HIP); //attaches the servo on pin 10 to the right hip 

  //Set initial position of motors
  myservo_0.write(90);
  myservo_1.write(90);
  myservo_2.write(90);
  myservo_3.write(90); 

  //Delay
  delay(5000); //5 second delay
}

void loop() {
  
  //Put your main code here, to run repeatedly:
  //Call functions here.
  example_Function();
}

//=============================================
//=============================================
//FUNCTION DEFINITIONS
//=============================================
//=============================================

//FUNCTION NAME: Example function
//DESCRIPTION: 
/*   
 Add information Describing the function here:
 This is an example function.This header can be
 copied for each individual function where a 
 description of the function of the function 
 can be stated.
*/
//=============================================
//ADD FUNCTION HERE
void example_Function(){
  
  Serial.println("This is the exmaple function call..."); 
  //Delay
  delay(1000);
}
//=============================================



//=============================================
//END OF PROGRAM
//=============================================

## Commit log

2017-02-19 Add sample code and first template
    Added sample code for MIIA that implements basic functionality. Also
    added the most basic template for getting started with programming MIIA.
2017-02-20 Add servo calibration code
    Added a code file that details the servo motor calibration. This is used
    in the associated video tutorial.
2017-10-15 Patch servo bug and add servo calibration pin
    [LOFI_MiiA_firmware.ino]
2017-10-17 Fix various issues with the MiiA LoFi Firmware. Now fully functional with Arduino Nano.
    [LOFI_MiiA_firmware.ino]
2017-10-26 Fix communication jitter issue
    Increased the interval to fix the communication jitter bug that saw
    commands being sent slowly to the microcontroller from LoFi blocks.
    [LOFI_MiiA_firmware.ino]
2017-11-26 Uploade MiiA assembly instruuctions update
    New instructions for the assmebly of MiiA
2019-07-07 Update README.md
    Credit Ottodiy and open source the CAD files
2019-07-07 Add Cad files
    Open source of Miia bot under the creative commons license
    [Bottom_assemV2.SLDASM, Bottom_bodyV2.SLDPRT, Bottom_frontalsV2.SLDPRT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]
